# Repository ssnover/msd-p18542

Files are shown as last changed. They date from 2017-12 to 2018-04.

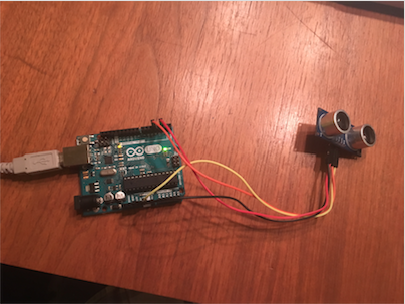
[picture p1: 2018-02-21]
prototyping/HCSRO4_Example/HCSR04 Wiring.png

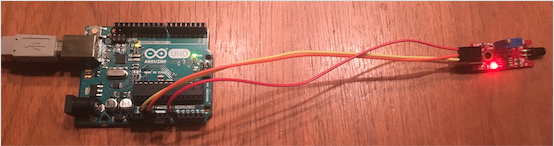
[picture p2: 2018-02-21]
prototyping/FlameSensor_Example/Flame sensor wiring.png

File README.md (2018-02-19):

# msd-p18542
Repository for RIT MSD P18542 source code, schematics, and CAD models.
# P18542: Real Time Terrain Mapping
In search and rescue operations time is often of the essence and the terrain can end up being wildly different than expected. The ability to image a landscape and use this data to determine the quickest route for operatives driving vehicles in this changing terrain in real-time could save lives in these scenarios. The goal of this project is to lay groundwork on this idea by imaging an area in real-time and using the image to plot route for a small autonomous vehicle.

## ASAR Robot
The first portion of this project consists of the electrical and PCB schematics for the robot along with mechanical CAD drawings and firmware for the Teensy 3.2 microcontroller development board.

### ASAR Teensy Firmware
The source code for the applications running on the Teensy is written for C++11 and will be made up of three primary applications run on a system tick:
1. Search and Rescue - controls search for the survivor and collection of data
2. Locomotion - controls movement of the robot
3. Command Manager - interfaces to the ASAR Aerial Platform to receive commands

## ASAR Aerial Platform
The second major portion of the project is a series of Python 3 modules run on a Raspberry Pi 3. These present a GUI for running the simulation and algorithms related to the computer vision and path finding aspects of the project. The major components include:
1. `asar-camera-engine` - Interface to the Raspberry Pi Camera
2. `asar-vision` - Generates a terrain map model from images
3. asar-path-finder - Takes the map model and finds the quickest path between two points
4. asar-web-ui - A web app hosted on the Pi to act as a GUI
5. asar-comms-server - Interface to the Pi's hardware UART
6. asar-core - The application the controls the flow of data between all of the above

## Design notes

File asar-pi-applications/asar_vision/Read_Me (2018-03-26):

# _Automatic Image Processing_ 
**Calibration Routine**
* This needs to be ran at the very beginning of a simulation.
* The calibration routine will walk you through clicking each individual color as well as the corners of the terrain in case of automation failure
* Once the calibration is done, the values printed out for color need to be input into the "Get RGB code"
* The corners of the terrain need to be input into the destination points backup for the homography
* This only needs to be done once unless the camera is bumped moving it significantly from its original position.

**Homography Automated**
* This is the main script that can be called.
* Within this file, all of the attributes of the terrain will be found and returned.
* An image is received from the raspberry pi that will the be processed. 
* After all processing is done, the tile attributes will be packaged into a json file named "Terrain.txt" and then sent to the path planning algorithm.

**Four Corners**
* The four corners of the terrain are automatically identified and marked as the source points for the image perspective transformation.
* This is where the hardcoded values that were obtained in the calibration routine will be held in the case that the corners are not able to be automatically found.

**Get Attributes**
* This script is responsible for finding all important parameters of the terrain.
* Within it, the color and coordinates of each tile are found.

**Get Coordinates**
* This script takes in the pixel values of each centroid of the hexagons within the terrain and classifies them as specific coordinats (1-8,1-8) on the grid for easier referencing.
* Once all nodes are classified, the coordinated values are added to the "coordinate" key in the hexagon attribute dictionary.

**Get RGB Color**
* This script gets the average pixel color value in the center of each identified hexagon
* Once the average HSV pixel color is found, it is converted to RGB and classified as one of the predetermined colors that were found in the calibration routine.
* The identified colors are added to the "Color" key within the hexagon attributes dictionary.

**Get Missing Terrain**
* This script looks at the coordinate list that was made by identifying hexagons on the terrain and compares it to the ideal coordinate list where all hexagons are found.
* If there are any missing points, the coordinate list is appended with the missing value and the color list is appended with an impassable terrain. If we dont know what is there, we cannot travel through it safely.

**Detect Shapes**
* This is the script responsible for finding the shapes within the terrain by finding the contour and counting the verticies.

**Shape Detection Test**
* If the shapes are not being identified, you can see exactly what the camera is seeing by running the image through this test script.

**Real Time HSV Codes**
* When Making masks, this script can be used to see what the mask will do block out or pass. The slider bars on the top are used to adjust the HSV values.

**Converter**
* This is used to make the upper and lower bounds of the masks that you make using the real time HSV code script.

**Utils**
* This allows you to clock the image in the calibration routine and have it return the values for the four corners to you as well as showing you where you clicked.

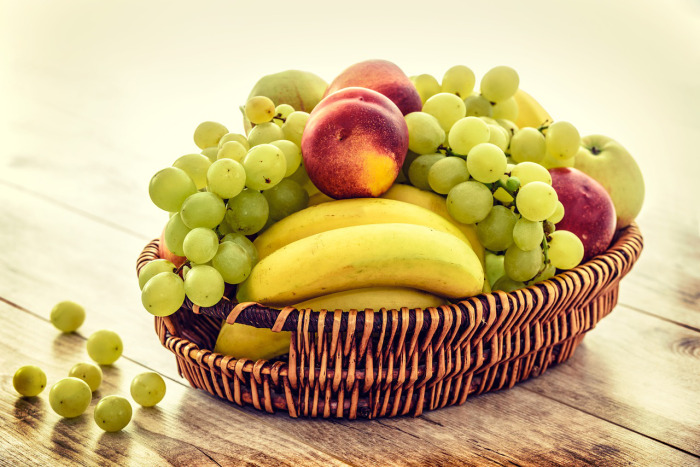
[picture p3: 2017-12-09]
prototyping/OpenCv/FruitBasket.jpg

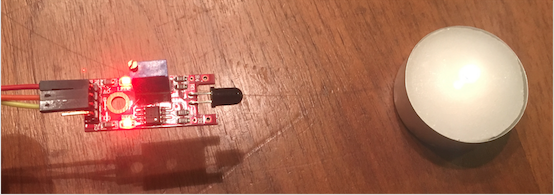
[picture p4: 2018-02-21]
prototyping/FlameSensor_Example/Flame detected.png

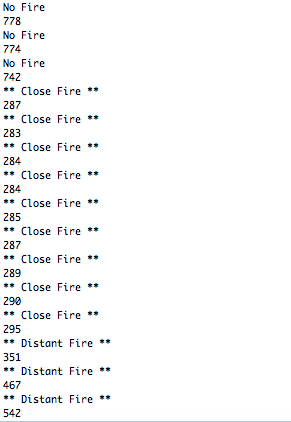
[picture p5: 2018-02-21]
prototyping/FlameSensor_Example/Flame Sensor Serial Output.png

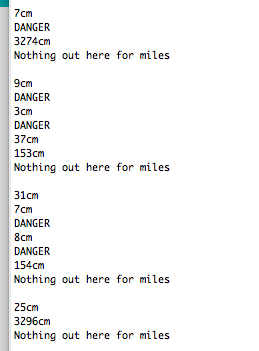
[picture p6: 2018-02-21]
prototyping/HCSRO4_Example/Ultrasonic Serial Output Example.png

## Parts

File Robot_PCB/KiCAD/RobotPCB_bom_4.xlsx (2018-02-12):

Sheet: imported
Component | Description | Part | References | Value | Footprint | Quantity Per PCB | Datasheet | P/N | MFG | Decription | Cost | Descrpition
1 | Unpolarized capacitor | C | C2 C3 | .1uF | C_1206_HandSoldering | 2 |  | GRM319R71H104KA01D | Murata | CAP CER 0.1UF 50V X7R 1206 | 0.26
2 | CAP CER 0.33UF 50V X7R 1206 | C | C1 | .33uF | C_1206_HandSoldering | 1 |  | GRM319R71H334KA01D | MURATA |  | 0.44
3 | LED GRN DIFF 5MM ROUND T/H | LED | D1 D2 D3 D4 | LED_GRN | LED_D5.0mm | 4 |  | LTL-4233 | Lite-On Inc. |  | 0.36
4 | PTC RESET FUSE 16V 2A RADIAL | Fuse | F1 F2 F3 F4 | 16V_2A | RHEF100 | 4 |  | RHEF200 | Littlefuse Inc. |  | 0.6
5 | CONN HEADER FEMALE 14POS.1" TIN | CON14_TeensyLeft | J1 | CON14_TeensyLeft | Socket_Strip_Straight_1x14_Pitch2.54mm | 1 |  | PPTC141LFBN-RC | Sullins Connector |  | 0.91
6 | CONN HEADER FEMALE 14POS.1" TIN | CON14_TeensyRight | J2 | CON14_TeensyRight | Socket_Strip_Straight_1x14_Pitch2.54mm | 1 |  | PPTC141LFBN-RC | Sullins Connector |  | 0.91
7 | CONN HEADER PH TOP 2POS 2MM | CON2_Battery | J11 | CON2_Battery | JST_PH_B2B-PH-K_02x2.00mm_Straight | 1 |  | B2B-PH-K-S(LF)(SN | JST Sales America Inc |  | 0.17
8 | CONN HEADER RTANG 2POS PCB TIN | CON2_DC-MOTOR | J7 J8 | CON2_DC-MOTOR | 5-103634-1 | 2 |  | 5-103634-1 | TE Connectivity |  | 0.73
9 | CONN HEADER RTANG 3POS PCB TIN | CON3_Servo | J9 | CON3_Servo | 5-103634-2 | 1 |  | 5-103634-2 | TE Connectivity |  | 1.11
10 | CONN HEADER RTANG 5POS PCB TIN | CON5_HC-SR04 | J3 | CON5_HC-SR04 | 5-103634-4 | 1 |  | 5-103634-4 | TE Connectivity |  | 1.32
11 | CONN HEADER FEM 5POS .1" SGL TIN | CON5_XBEE | J10 | CON5_XBEE | Socket_Strip_Straight_1x05_Pitch2.54mm | 1 |  | PPTC051LFBN-RC | Sullins Connector |  | 0.47
12 | CONN HEADER RTANG 6POS PCB TIN | CON6_M-Encoder | J5 J6 | CON6_M-Encoder | 5-103634-5 | 2 |  | 5-103634-5 | TE Connectivity |  | 1.4
13 | CONN HEADER RTANG 4POS PCB TIN | Con4_FlameSensor | J4 | Con4_FlameSensor | 5-103634-3 | 1 |  | 5-103634-3 | TE Connectivity |  | 1.3
14 | CONN HEADER .100" SNGL STR 15POS | TestHeaders | J12 J13 | TestHeaders | Pin_Header_Straight_1x15_Pitch2.54mm | 2 |  | PRPC015SAAN-RC | Sullins Connector |  | 0.38
15 | RES SMD 0 OHM JUMPER 1/4W 1206 | R | R6 R7 | R_0 | R_1206_HandSoldering | 2 |  | RC1206JR-070RL | Yageo |  | 0.1
16 | RES SMD 150 OHM 5% 1/4W 1206 | R | R3 | R_150 | R_1206_HandSoldering | 1 |  | RC1206JR-07150RL | Yageo |  | 0.1
17 | Resistor | R | R1 R2 | R_1K | R_1206_HandSoldering | 2 |  | RC1206JR-071KL | Yageo |  | 0.1 | RES SMD 1K OHM 5% 1/4W 1206
18 | RES SMD 59 OHM 1% 1/4W 1206 | R | R4 R5 | R_59 | R_1206_HandSoldering | 2 |  | RC1206FR-0759RL | Yageo |  | 0.1
19 | AUDIO PIEZO TRANSDUCER 30V TH | Speaker | SP1 | Speaker | BUZZER | 1 |  | PS1240P02BT | TDK |  | 0.72
20 | SWITCH TOGGLE SPDT 5A 120V | SW_SPST | SW1 | SW_SPST | WireConnection_1.20mmDrill | 1 |  | 100SP1T1B1M1QEH | E-Switch |  | 2.11
21 | IC MOTOR DRIVER PAR 16-DIP | L293D | U2 | L293D | L293D | 1 |  | L293D | ST Microelectronics |  | 3.91
22 | IC REG LINEAR 5V 1.5A TO220AB | L7805 | U1 | L7805 | TO-220 | 1 | http://www.st.com/content/ccc/resource/technical/document/datasheet/41/4f/b3/b0/12/d4/47/88/CD00000444.pdf/files/CD00000444.pdf/jcr:content/translations/en.CD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 | L7805CV | STMicroelectronics |  | 0.45
Component Groups: | 22
Component Count: | 35
Fitted Components: | 35
Number of PCBs: | 1
Total components: | 35
Schematic Version: | 4
Schematic Date: | 2018-02-07
BoM Date: | 2018-02-12 14:37
Schematic Source: | C:/Users/ME/Documents/School/Spring_2018/Senior Design/Schematic/Kicad/RobotPCB.sch
KiCad Version: | Eeschema 4.0.7

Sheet: Better BOM
Board
 | Component | Quantity | References | Value | P/N | MFG | Cost | Ext. Cost
 | 1 | 2 | C2 C3 | .1uF | GRM319R71H104KA01D | Murata | $0.26 | $0.52
 | 2 | 1 | C1 | .33uF | GRM319R71H334KA01D | MURATA | $0.44 | $0.44
 | 3 | 4 | D1 D2 D3 D4 | LED_GRN | LTL-4233 | Lite-On Inc. | $0.36 | $1.44
 | 4 | 4 | F1 F2 F3 F4 | 16V_2A | RHEF200 | Littlefuse Inc. | $0.60 | $2.40
 | 5 | 1 | J1 | CON14_TeensyLeft | PPTC141LFBN-RC | Sullins Connector | $0.91 | $0.91
 | 6 | 1 | J2 | CON14_TeensyRight | PPTC141LFBN-RC | Sullins Connector | $0.91 | $0.91
 | 7 | 1 | J11 | CON2_Battery | B2B-PH-K-S(LF)(SN | JST Sales America Inc | $0.17 | $0.17
 | 8 | DNI | J7 J8 | CON2_DC-MOTOR | 5-103634-1 | TE Connectivity | $0.73 | $0.00
 | 9 | 1 | J9 | CON3_Servo | 5-103634-2 | TE Connectivity | $1.13 | $1.13
 | 10 | 1 | J3 | CON5_HC-SR04 | 5-103634-4 | TE Connectivity | $1.34 | $1.34
 | 11 | 1 | J10 | CON5_XBEE | PPTC051LFBN-RC | Sullins Connector | $0.47 | $0.47
 | 12 | 2 | J5 J6 | CON6_M-Encoder | 5-103634-5 | TE Connectivity | $1.47 | $2.94
 | 13 | 1 | J4 | Con4_FlameSensor | 5-103634-3 | TE Connectivity | $1.32 | $1.32
 | 14 | 2 | J12 J13 | TestHeaders | PRPC015SAAN-RC | Sullins Connector | $0.38 | $0.76
 | 15 | 2 | R6 R7 | R_0 | RC1206JR-070RL | Yageo | $0.10 | $0.20
 | 16 | 1 | R3 | R_150 | RC1206JR-07150RL | Yageo | $0.10 | $0.10
 | 17 | 2 | R1 R2 | R_1K | RC1206JR-071KL | Yageo | $0.10 | $0.20
 | 18 | 2 | R4 R5 | R_59 | RC1206FR-0759RL | Yageo | $0.10 | $0.20
 | 19 | 1 | SP1 | Speaker | PS1240P02BT | TDK | $0.72 | $0.72
 | 20 | 1 | SW1 | SW_SPST | 100SP1T1B1M1QEH | E-Switch | $2.11 | $2.11
 | 21 | 1 | U2 | L293D | L293D | ST Microelectronics | $3.91 | $3.91
 | 22 | 1 | U1 | L7805 | L7805CV | STMicroelectronics | $0.57 | $0.57
 |  |  |  |  |  |  | Board total | $22.76
Cables
 | Cable | Part | MFG | MFG # | Quantity per cable | Cost ea | Ext Cost per cable | Total Quantity | Total Cost
 | Motor (x2)
 |  | Female Pins | TE Connectivity | 1-104480-7 | 6 | 0.164 | $0.98 | 12 | $1.97
 |  | 6p Female Header | TE Connectivity | 104257-5 | 1 | 0.68 | $0.68 | 2 | $1.36
 | HC-SR04
 |  | Female Pins | TE Connectivity | 1-104480-7 | 4 | 0.164 | $0.66 | 4 | $0.66
 |  | 5P Female Header | TE Connectivity | 104257-4 | 1 | 0.6 | $0.60 | 1 | $0.60
 | Flame Sensor
 |  | Female Pins | TE Connectivity | 1-104480-7 | 4 | 0.164 | $0.66 | 4 | $0.66
 |  | 4P Female Header | TE Connectivity | 104257-3 | 1 | 0.58 | $0.58 | 1 | $0.58
 | Servo
 |  | Female Pins | TE Connectivity | 1-104480-7 | 3 | 0.164 | $0.49 | 3 | $0.49
 |  | 3P Header | TE Connectivity | 104257-3 | 1 | 0.52 | $0.52 | 1 | $0.52
 | Battery
 |  | Female Pins | JST | SPH-002T-P0.5L | 2 | 0.1 | $0.20 | 2 | $0.20
 |  | Female Housing | JST | PHR-2 | 1 | 0.1 | $0.10 | 1 | $0.10
 |  |  |  |  |  |  |  | Total Cable Cost | $7.13
 |  |  |  |  |  |  | Total | $29.89
 | Cable Totals | Part | MFG | P/N | Quatity | Cost | Ext Cost
 |  | Female Pins | TE Connectivity | 1-104480-7 | 23 | 0.164 | $3.77
 |  | Female pins | JST | SPH-002T-P0.5L | 2 | 0.1 | $0.20
 |  | 6p header | TE Connectivity | 104257-5 | 2 | 0.68 | $1.36
 |  | 5p header | TE Connectivity | 104257-4 | 1 | 0.6 | $0.60
 |  | 4p header | TE Connectivity | 104257-3 | 1 | 0.58 | $0.58
 |  | 3pheader | TE Connectivity | 104257-2 | 1 | 0.52 | $0.52
 |  | 2p header | JST | PHR-2 | 1 | 0.1 | $0.10
 |  |  |  |  |  | Total | $7.13

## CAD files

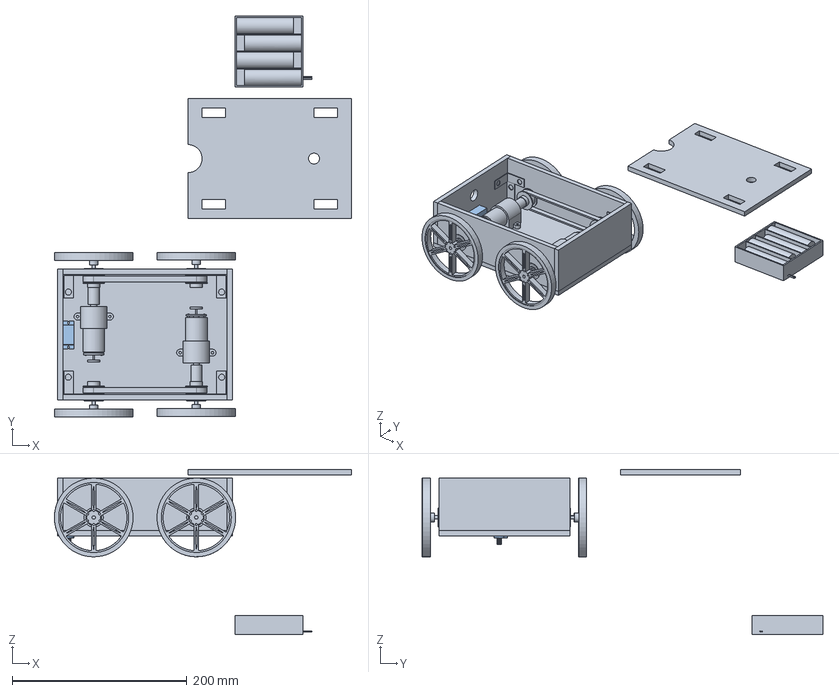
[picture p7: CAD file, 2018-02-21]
Robot-Design/Assembly 1 (1).step
339.8 x 458.4 x 188.8 mm
DriveShaft
ServoBody

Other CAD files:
Robot-Design/4mm ROD LONG.sldprt
Robot-Design/WHEEL HUB.sldprt
Robot-Design/SHAFT COUPLER.sldprt
Robot-Design/BACK WALL (1).sldprt
Robot-Design/TIMING BELT PULLEY.sldprt
Robot-Design/MOTOR MOUNT.sldprt
Robot-Design/BEARING.sldprt
Robot-Design/SIDE WALLS (1).sldprt
Robot-Design/BASE (1).sldprt
Robot-Design/L-BRACKET.sldprt
Robot-Design/4mm ROD SHORT.sldprt
Robot-Design/SHELF.sldprt
Robot-Design/FRONT WALL (1).sldprt
Robot-Design/TIMING BELT.sldprt
Robot-Design/WHEELS.sldprt
Robot-Design/BEARING AXEL FITTING.sldprt
Robot-Design/MOTOR 34-1.sldprt
Robot-Design/18650 4S Battery Holder.sldprt

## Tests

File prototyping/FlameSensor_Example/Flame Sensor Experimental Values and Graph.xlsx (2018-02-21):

Distance | Analog Reading 1 | Analog Reading 2 | Analog Reading 3 | Analog Reading 4 | Analog Reading
5 | 288 | 285 | 283 | 284 | 285
10 | 289 | 289 | 290 | 292 | 290
15 | 301 | 299 | 296 | 295 | 297.75
20 | 301 | 303 | 310 | 303 | 304.25
25 | 407 | 452 | 438 | 463 | 440
30 | 550 | 561 | 562 | 578 | 562.75
35 | 644 | 655 | 649 | 650 | 649.5

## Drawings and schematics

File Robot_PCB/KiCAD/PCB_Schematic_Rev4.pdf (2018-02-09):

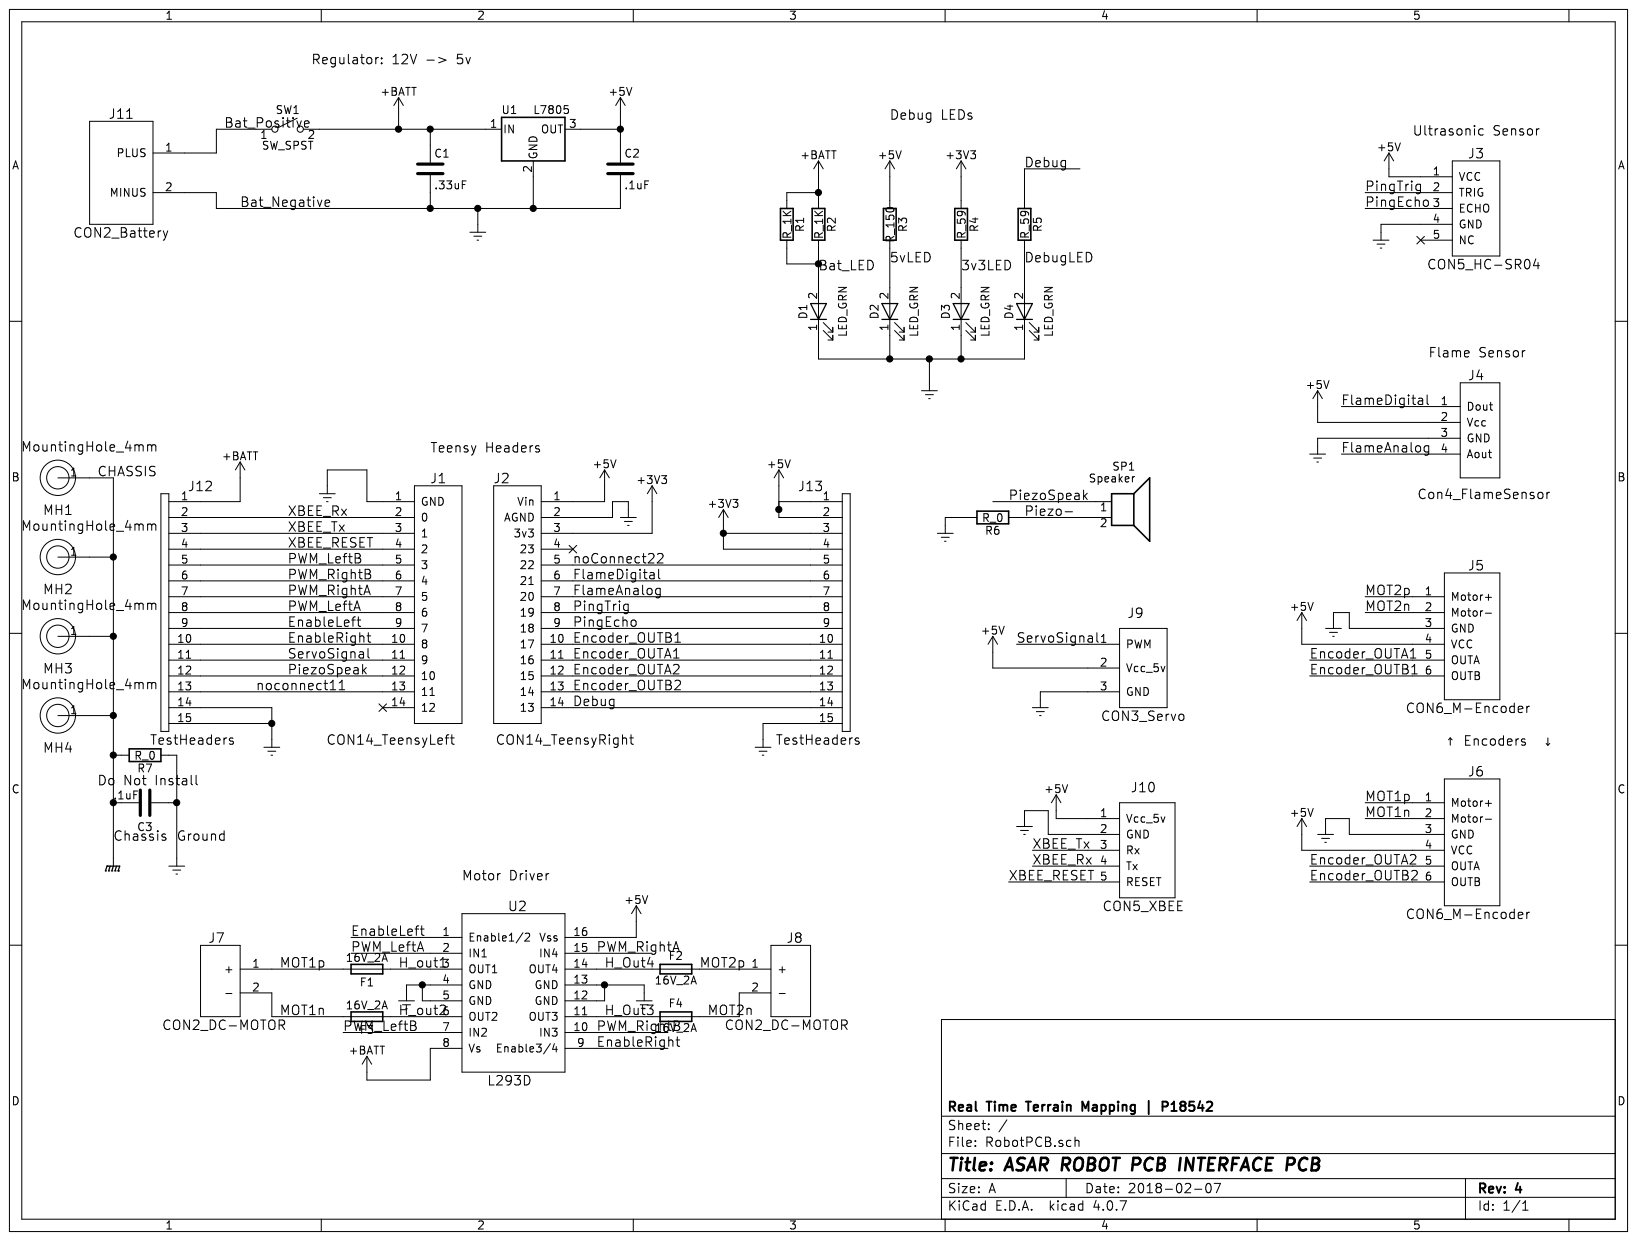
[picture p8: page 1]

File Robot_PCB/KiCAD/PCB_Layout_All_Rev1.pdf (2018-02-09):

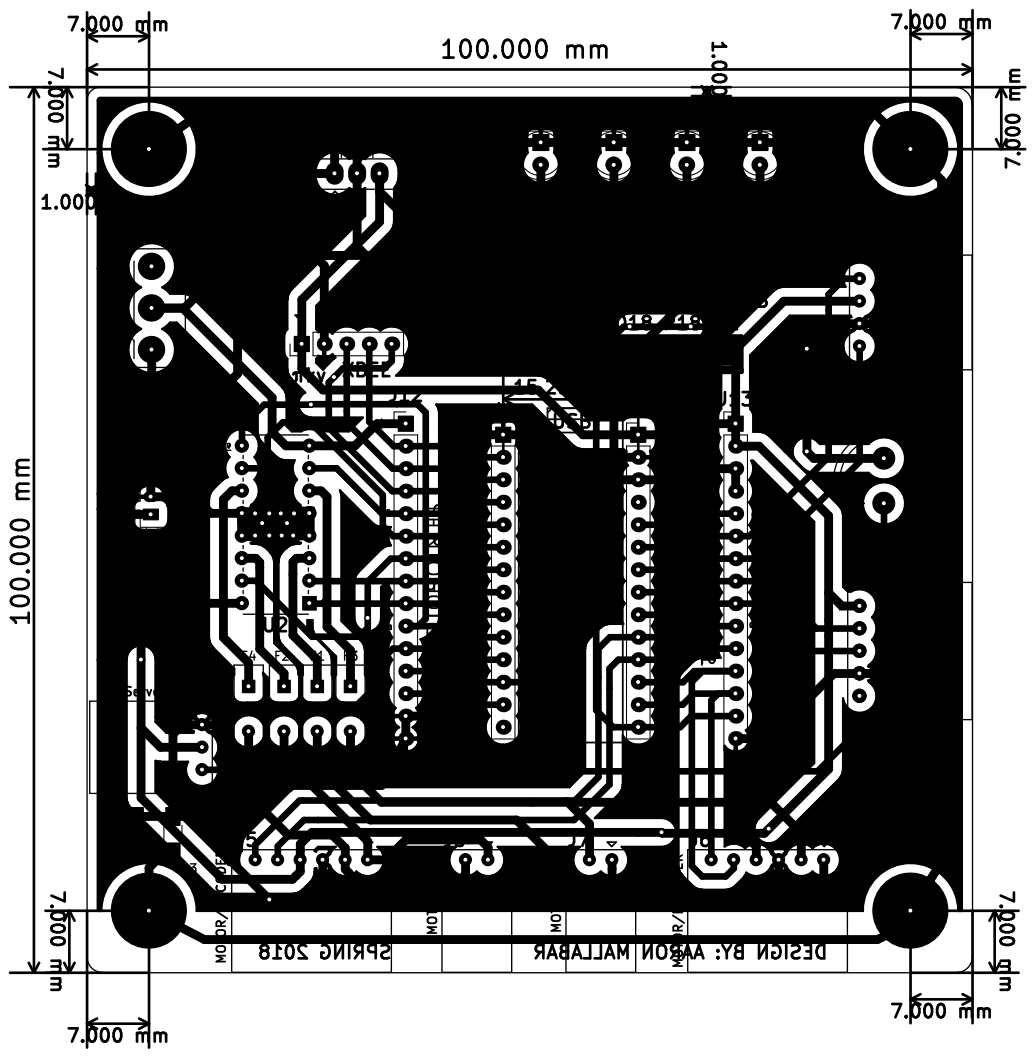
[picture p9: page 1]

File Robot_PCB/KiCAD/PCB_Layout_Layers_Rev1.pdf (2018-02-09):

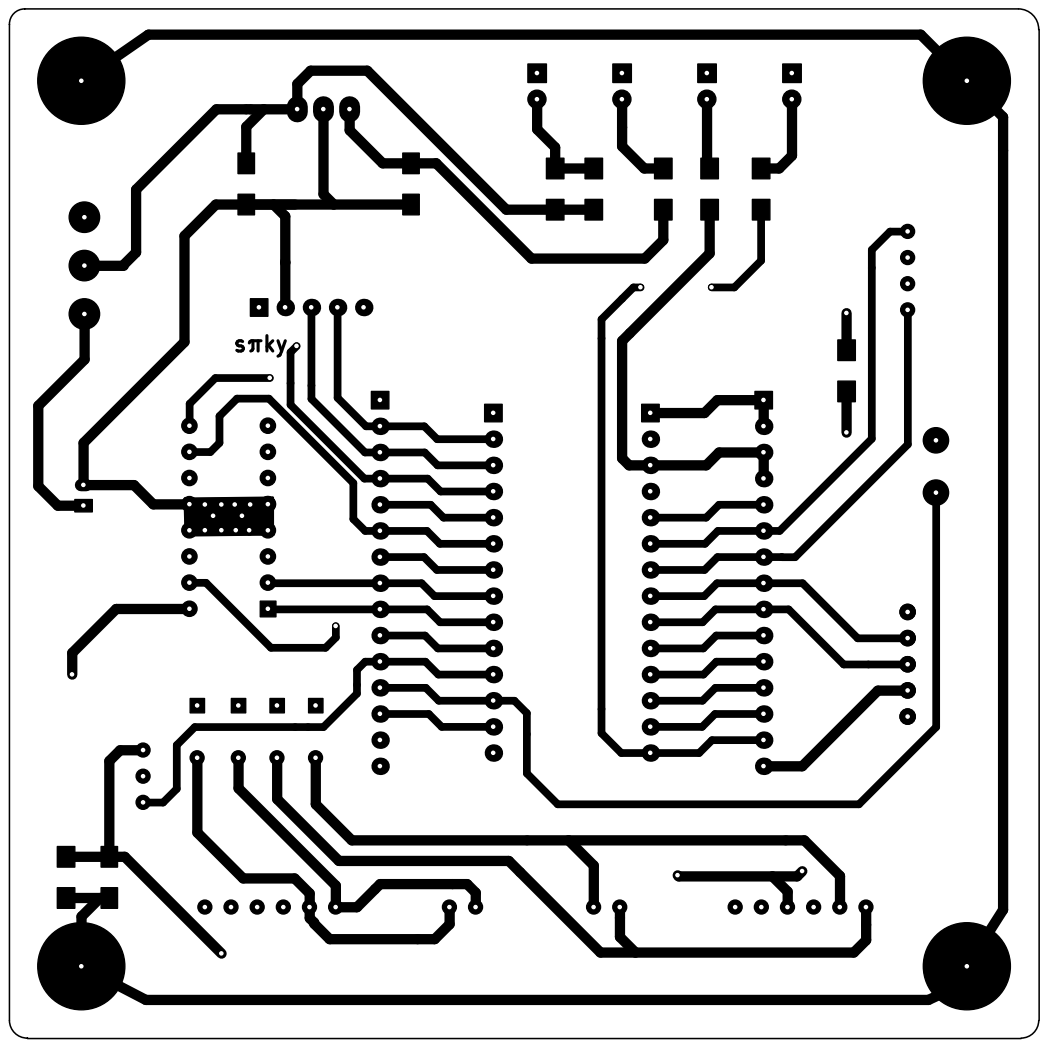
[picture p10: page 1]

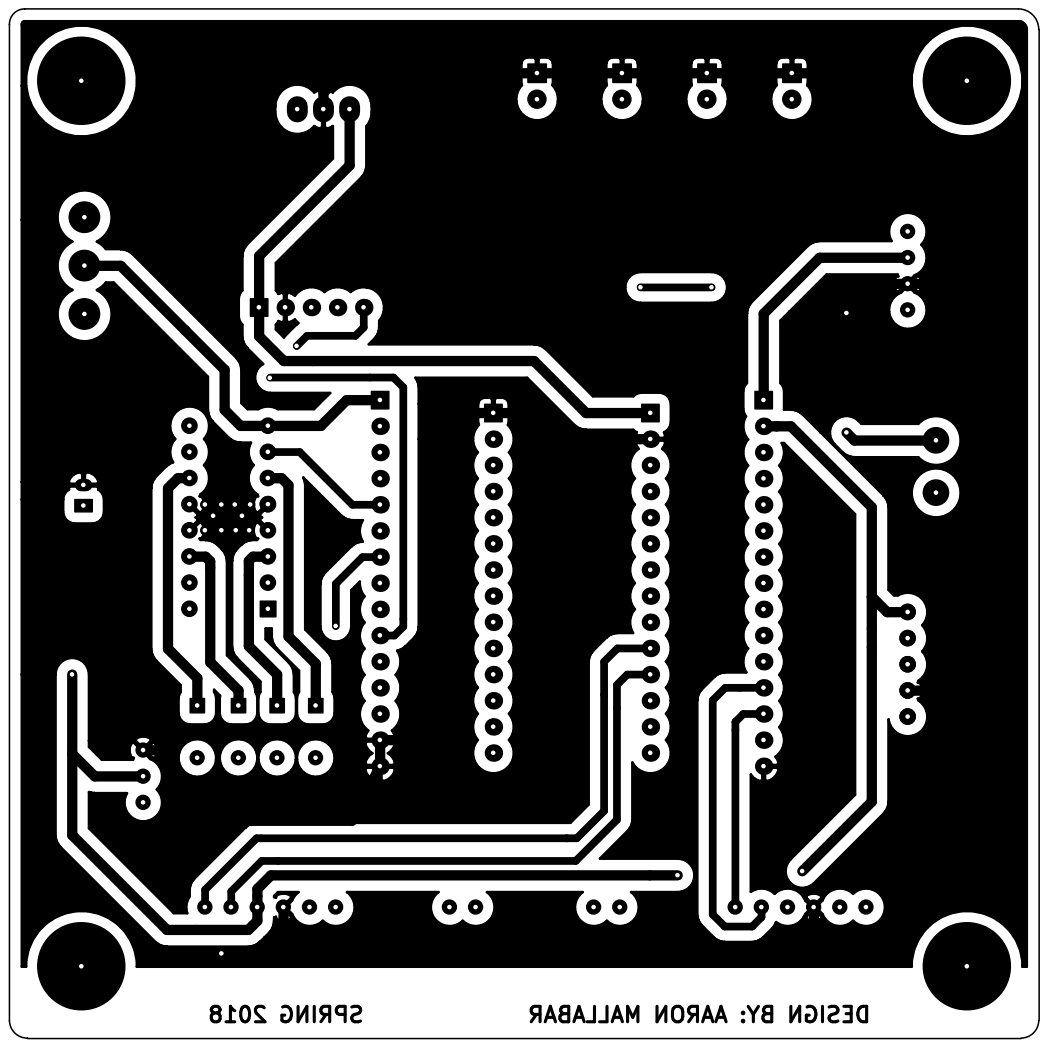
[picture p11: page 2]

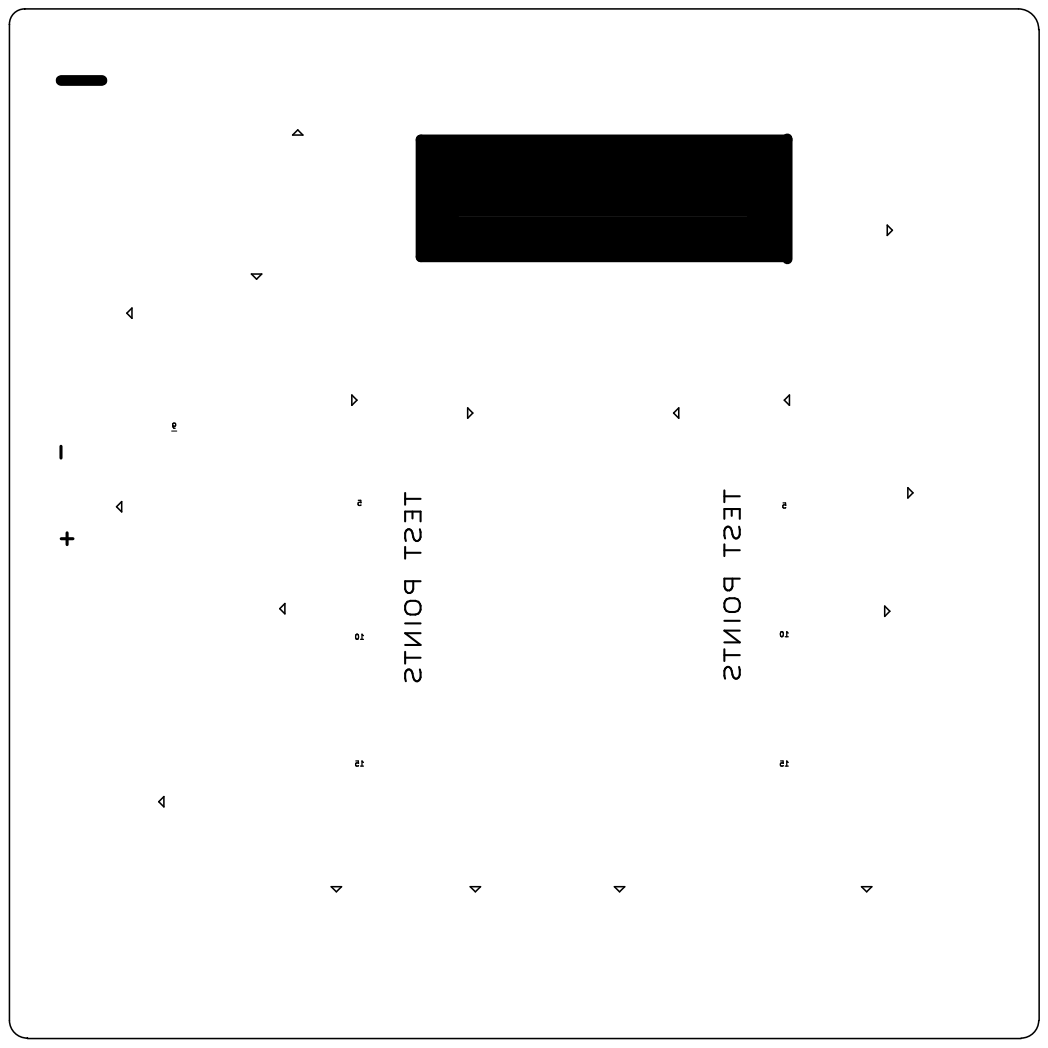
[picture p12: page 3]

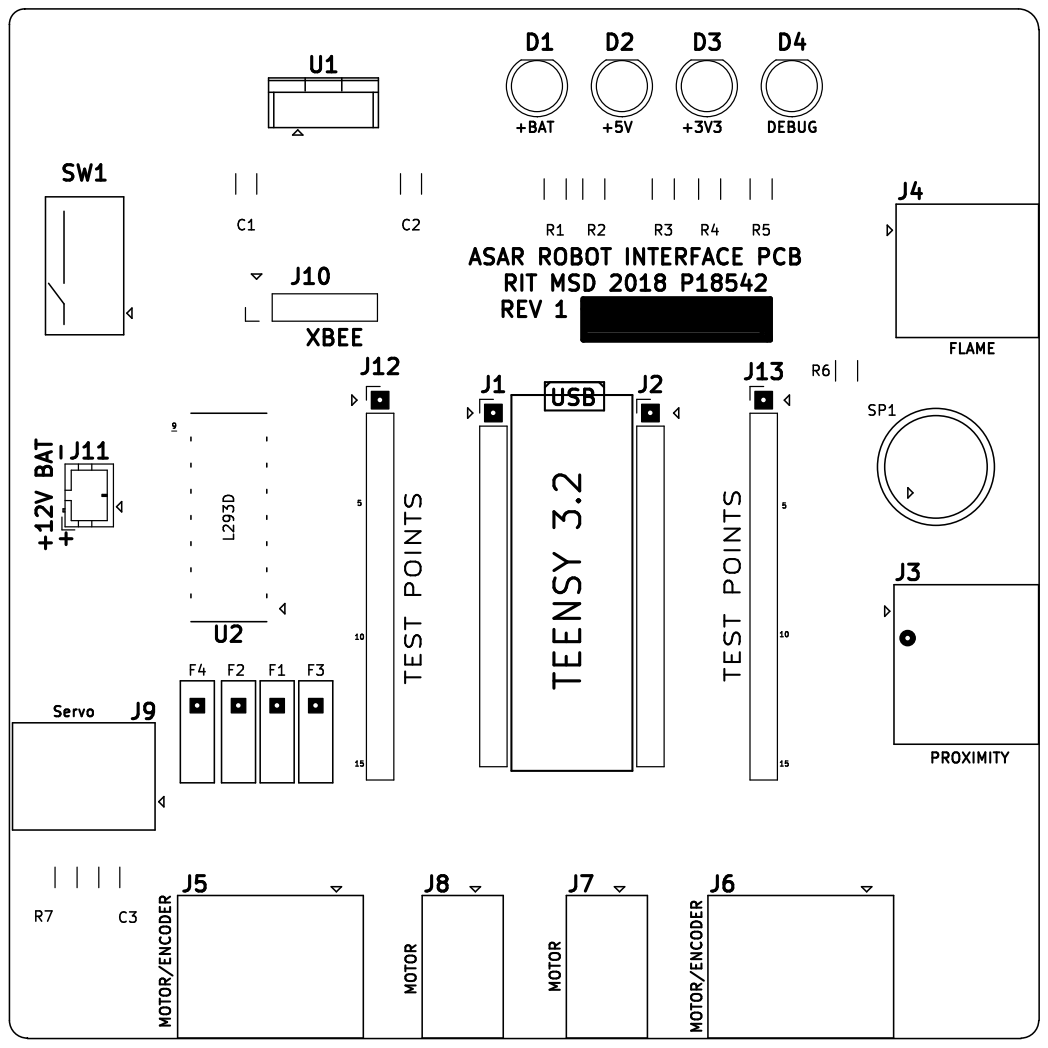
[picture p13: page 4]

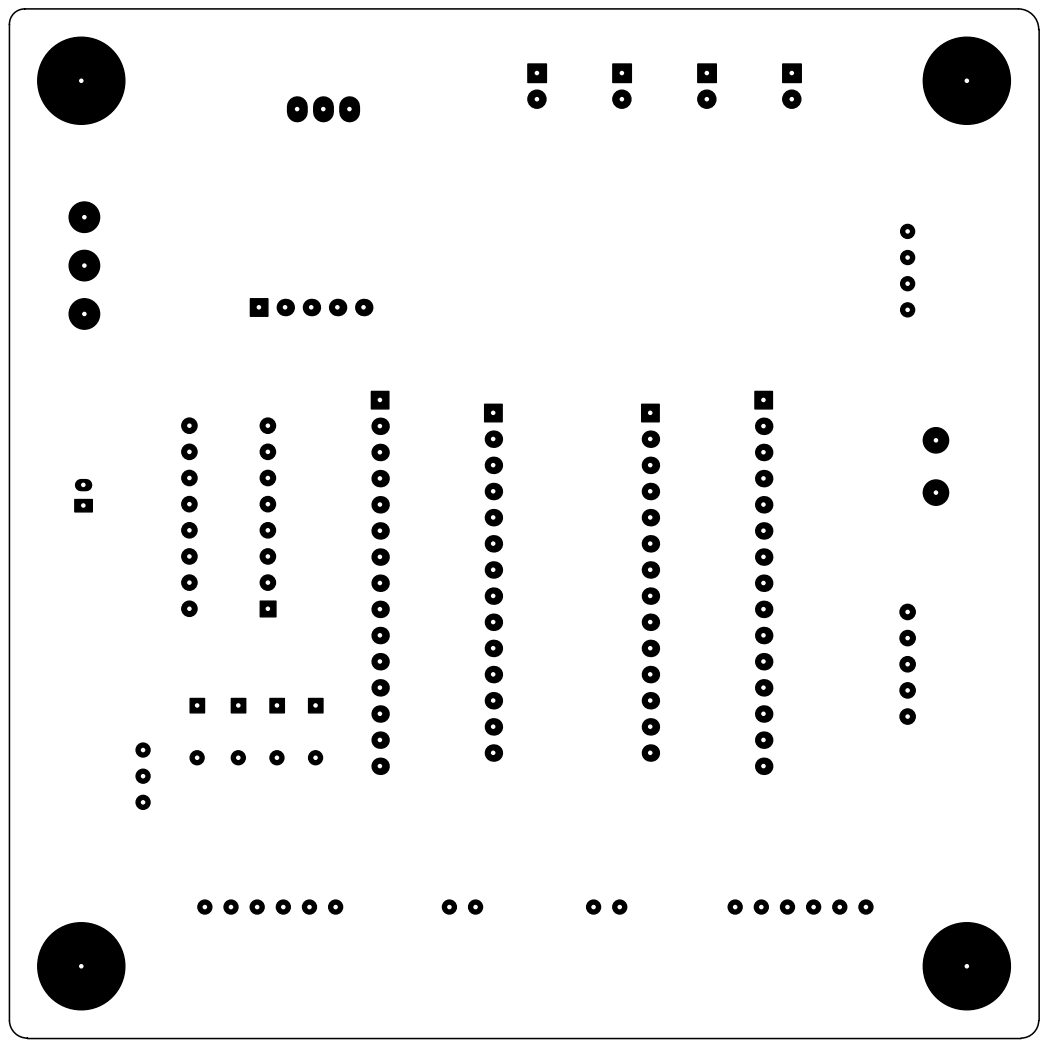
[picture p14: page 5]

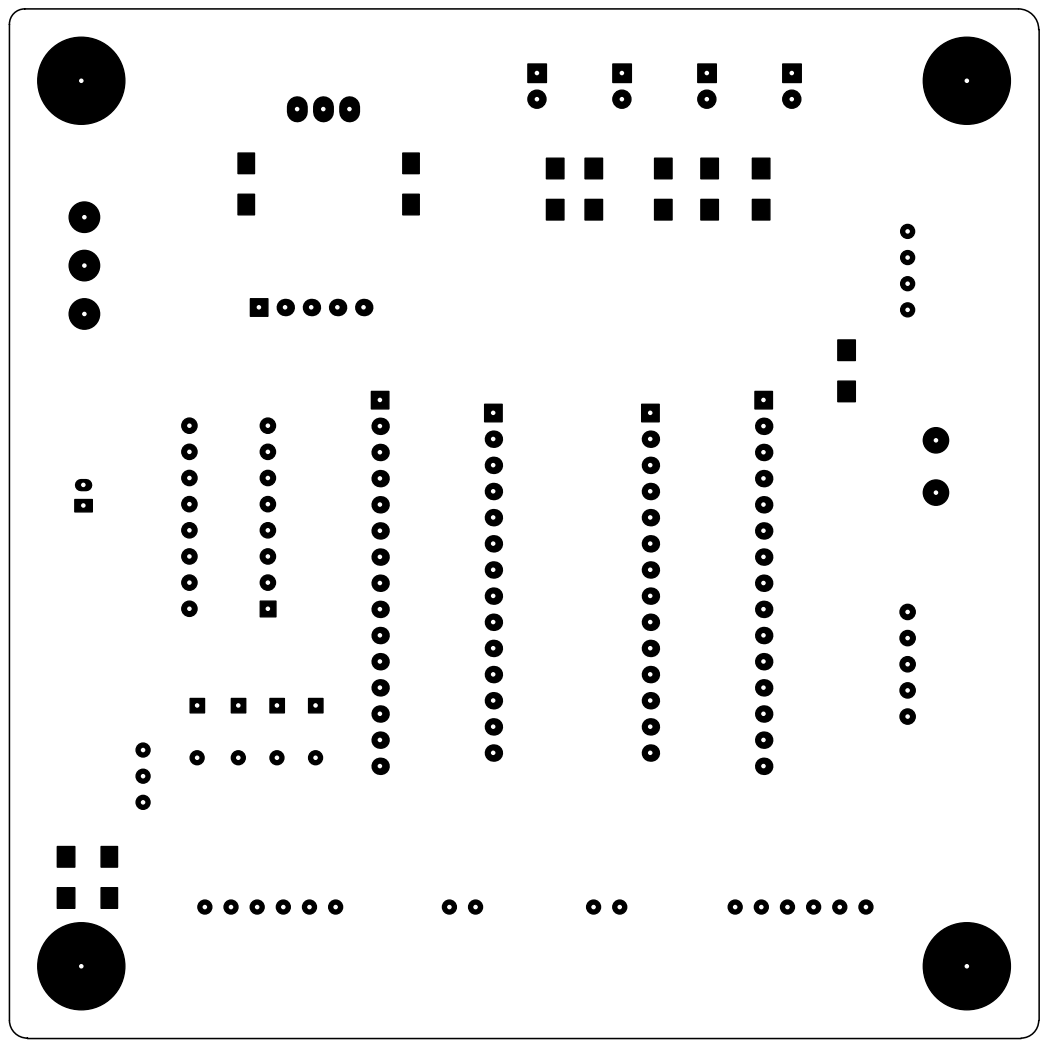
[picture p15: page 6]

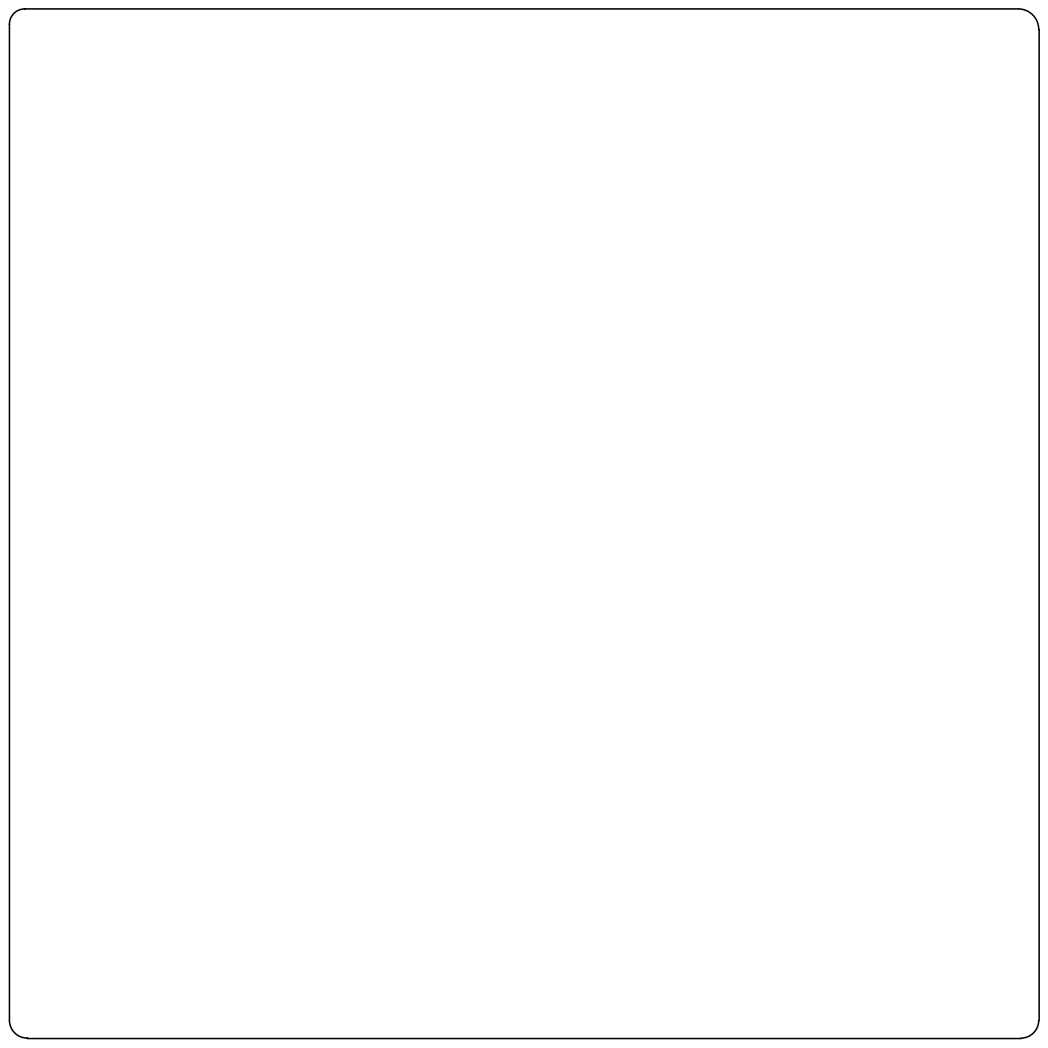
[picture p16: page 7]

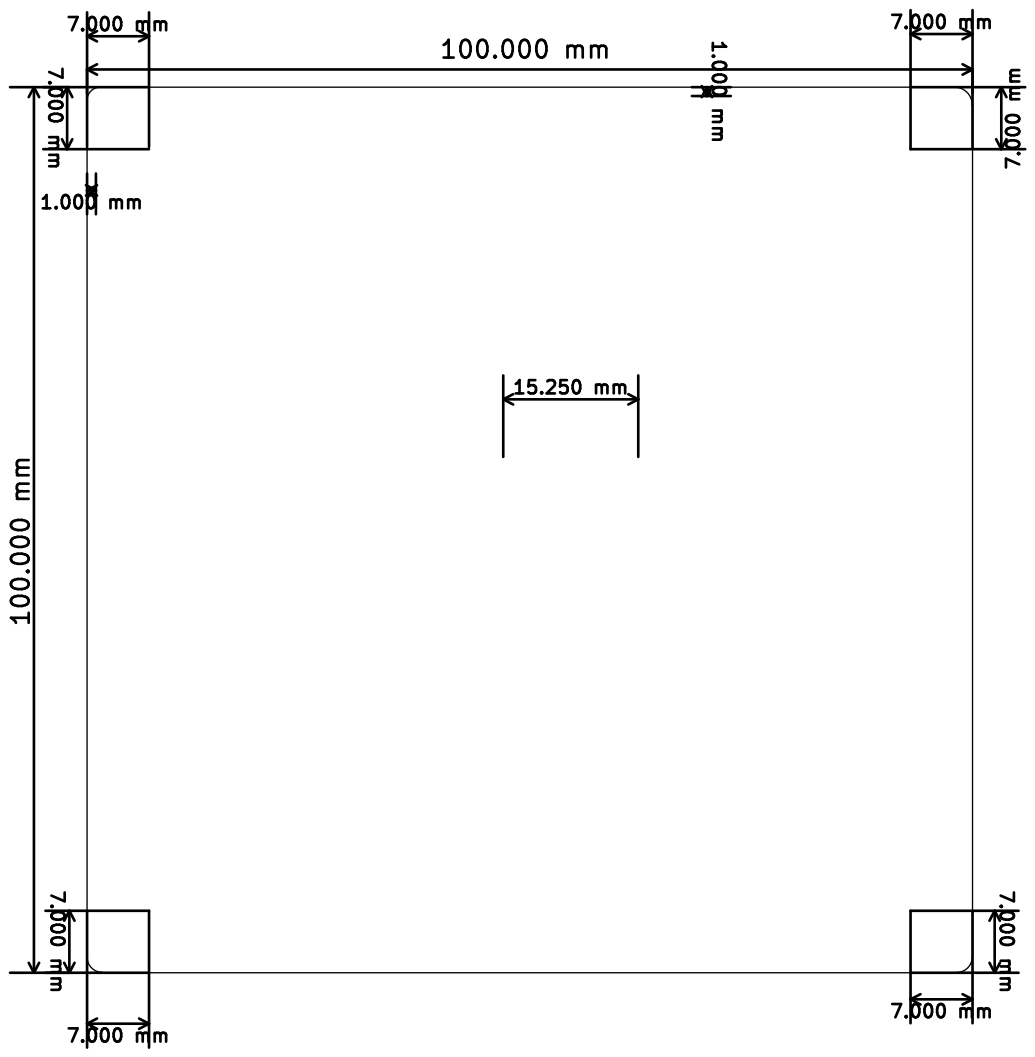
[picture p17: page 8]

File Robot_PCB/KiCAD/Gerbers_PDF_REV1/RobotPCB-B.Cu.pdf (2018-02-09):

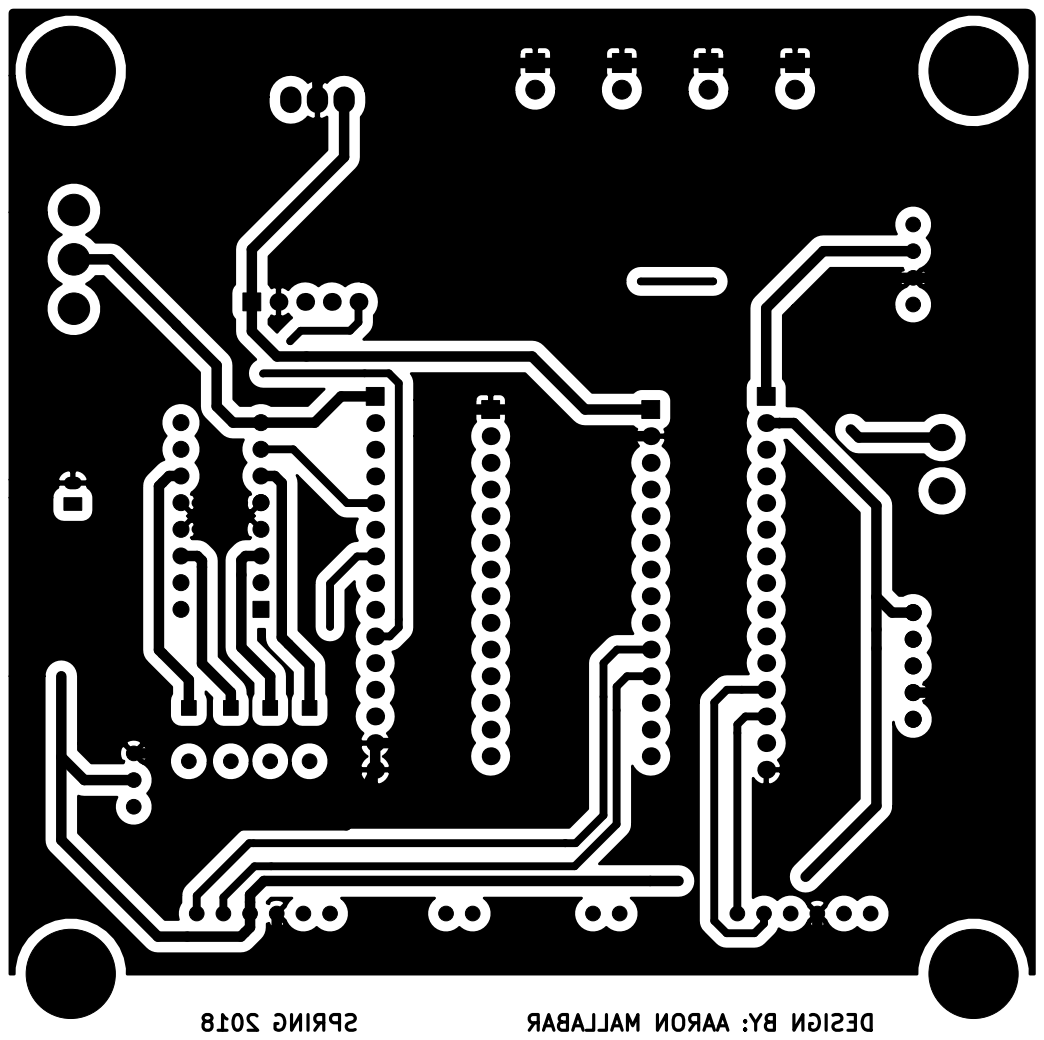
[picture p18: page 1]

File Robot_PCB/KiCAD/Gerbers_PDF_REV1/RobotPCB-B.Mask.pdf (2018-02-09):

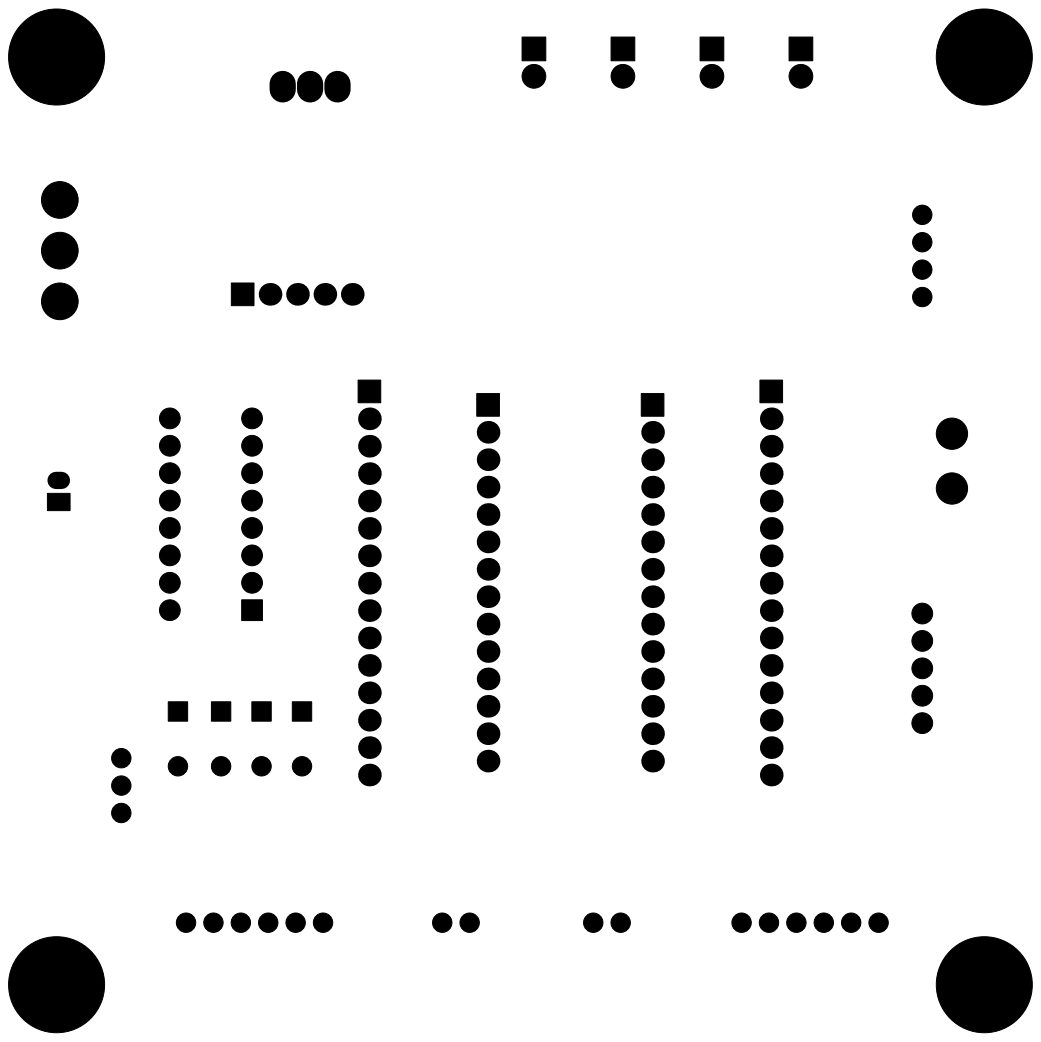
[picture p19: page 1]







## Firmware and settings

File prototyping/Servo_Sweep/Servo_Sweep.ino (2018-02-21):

Servo myservo;  // create servo object to control a servo
// twelve servo objects can be created on most boards

int pos = 0;    // variable to store the servo position

void setup() {
  myservo.attach(9);  // attaches the servo on pin 9 to the servo object
}

void loop() {
  for (pos = 0; pos <= 180; pos += 1) { // goes from 0 degrees to 180 degrees
    // in steps of 1 degree
    myservo.write(pos);              // tell servo to go to position in variable 'pos'
    delay(15);                       // waits 15ms for the servo to reach the position
  }
  for (pos = 180; pos >= 0; pos -= 1) { // goes from 180 degrees to 0 degrees
    myservo.write(pos);              // tell servo to go to position in variable 'pos'
    delay(15);                       // waits 15ms for the servo to reach the position
  }
}

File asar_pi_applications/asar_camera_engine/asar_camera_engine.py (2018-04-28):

#!/usr/bin/python3
"""
    file: asar-camera-engine.py
    purpose: Specifies the class for controlling and interfacing to the Raspberry Pi Camera.
"""

import datetime
import os
import sqlite3
import threading
import time


try:
    from picamera import PiCamera
except ImportError:
    print("PiCamera module is not installed.")
    quit()


class ASARCameraEngine:

    def __init__(self, frequency, database_store_call, image_path):
        """
        Constructor.
        """
        self.my_camera = PiCamera()
        self.my_capture_call = database_store_call
        self.my_images_directory = image_path
        self.my_capture_frequency = frequency
        self.my_worker_thread = threading.Thread(target=self.cameraEngineImageContext, args=())
        self.my_worker_thread.daemon = True
        self.my_running_status = False
        self.my_camera_is_busy = False

    def begin(self):
        """
        Start the thread controlling the ASAR camera engine.
        :return: Boolean representing the running state of the camera engine.
        """
        if self.my_camera_is_busy:
            return False
        self.my_running_status = True
        self.my_worker_thread.start()
        return True

    def end(self):
        """
        Stop the ASAR camera engine execution.
        :return: None.
        """
        print("Shutting down camera engine")
        self.my_running_status = False
        self.my_worker_thread.join()

    def takePicture(self):
        """
        Requests the engine to take a picture with the PiCamera.
        :return: Path to the image.
        """
        current_time = datetime.datetime.now()
        dt_string = '{:04d}'.format(current_time.year) \
                  + '{:02d}'.format(current_time.month) \
                  + '{:02d}'.format(current_time.day) \
                  + '_' \
                  + '{:02d}'.format(current_time.hour) \
                  + '{:02d}'.format(current_time.minute) \
                  + '{:02d}'.format(current_time.second) \
                  + '_' \
                  + '{:06d}'.format(current_time.microsecond)
        filename = dt_string + '.jpg'
        image_path = os.path.join(self.my_images_directory, filename)

        self.my_camera.capture(image_path, use_video_port=True)

        return image_path

    def takeVideo(self, path, length_in_seconds):
        """
        Requests the engine to take a video.
        :param path: The absolute path to the video file to create.
        :param length_in_seconds: Length of video to record in seconds.
        :return: Boolean of whether capture was started.
        """
        if path.split('.')[-1] != 'h264':
            return False
        if self.my_running_status:
            return False

        video_thread = threading.Thread(target=self.cameraEngineVideoContext,
                                        args=(path, length_in_seconds))
        video_thread.start()
        return True

    def cameraEngineImageContext(self):
        """
        Executed by the camera engine application to take a picture on a set rate.
        :return: None.
        """
        while self.my_running_status:
            print("Taking that picture!")
            # need to start putting image paths in database
            new_image_path = self.takePicture()

            time.sleep(1 / self.my_capture_frequency - 0.1)

    def cameraEngineVideoContext(self, path, length_in_seconds):
        """
        Executed by the camera engine application to take a video for a set
        amount of time.
        :param path: Path to store the video capture at.
        :param length_in_seconds:
        :return: None
        """
        self.my_camera_is_busy = True
        start_time = datetime.datetime.now()
        self.my_camera.start_recording(path)

        while (datetime.datetime.now() - start_time).seconds < length_in_seconds:
            pass

        self.my_camera.stop_recording()
        self.my_camera_is_busy = False


def main():
    """
    Entry point for testing.
    :return:
    """
    TOTAL_TIME_TO_RUN_SECONDS = 10
    CAPTURE_FREQUENCY_HZ = 2
    IMAGE_STORAGE_LOCATION = os.path.join(os.sep, 'home', 'pi', 'asar', 'images')

    my_camera = ASARCameraEngine(CAPTURE_FREQUENCY_HZ,
                                 os.path.join(os.sep, 'tmp', 'asar.db'),
                                 IMAGE_STORAGE_LOCATION)
    my_camera.begin()
    start_time = datetime.datetime.now()

    while (datetime.datetime.now() - start_time).seconds < TOTAL_TIME_TO_RUN_SECONDS:
        time.sleep(1)

    my_camera.end()

    for filename in os.listdir(IMAGE_STORAGE_LOCATION):
        if '.jpg' in filename:
            os.remove(os.path.join(IMAGE_STORAGE_LOCATION, filename))

    return 0


if __name__ == "__main__":
    main()

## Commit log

2017-11-13 Added prototyping for the wireless communications with the XBee.
2017-11-15 Fixed a function comment.
    [main.py]
2017-11-15 Created a socket wrapper and wrote simple code for the two sockets.
2017-11-15 Added a common source for prototypes.
2017-11-15 Add files via upload
    Rev 1 of the Schematic. Uses STM32.
    [MSD_ROBOT_BOARD.DSN]
2017-11-15 Moving Files Around
    [MSD_ROBOT_BOARD.DSN]
2017-11-30 REV2 Schematic Files: Uses TEENSY and XBEE
    [MSD_ROBOT_BOARD_REV2.DSN]
2017-12-06 Fixed edge case for 0x00. Made sketch for interpreting bytedata visually.
    [main.py, wireless-proto.ino]
2017-12-06 Added terminal switch for Pi.
2017-12-08 Fixed the device path for hardware UART on Pi. Tested and works.
    [main.py]
2017-12-08 Entry point for Teensy firmware.
2017-12-08 New Uploaded Files, Final for DDR
    [MSD_ROBOT_BOARD_REV2.DSN, MSD_ROBOT_BOARD_REV2.xlsx]
2018-01-08 KiCAD Files
    [RobotPCB.sch, RobotPCB_bom_3.xlsx]
2018-01-08 KiCAD Schematic
2018-01-08 deleted because of duplicates created trying to change the name
    [RobotPCB.sch, RobotPCB_bom_3.xlsx]
2018-01-13 Initial commit for asar-camera-engine application module.
2018-01-18 Initital Testing, BlinkLED Motor Forward
2018-01-18 Added Encoder Test
2018-01-22 Remove outdated schematic PDF
2018-01-22 MotorClass File Added
2018-01-22 Add Motor.H, Motor.cpp and modified test script to test motor
2018-01-24 More Motor Tests and Blinky program
2018-02-09 Board Update to REV1 Package
    Schematic Rev3 -> Rev4
    Layout Rev1 Final
    (Still need to update Bom)
    [RobotPCB-B.Cu.gbl, RobotPCB-B.Mask.gbs, RobotPCB-B.SilkS.gbo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]
2018-02-12 Updated to Rev4 and Purchased BOM
    [RobotPCB_bom_3.xlsx, RobotPCB_bom_4.xlsx]
2018-02-14 Complete function definitions in ASAR camera engine class
2018-02-18 Base frame of front end
2018-02-18 Fix thread joining mistake
    [asar_camera_engine.py]
2018-02-18 Fixed concurrency issue while using threads, changed to video due to speed concerns in taking pictures
    [asar_camera_engine.py]
2018-02-19 Good blink on interrupt script for teensy (Replaced the one that only worked for uno
    [good_blink.ino]
2018-02-19 Working Test Script for Proximity Sensor
2018-02-19 Added comments to ping test script and added a quick piezo buzzer test script
    [melodyScript.ino]
2018-02-19 Added Servo Test Script that works
2018-02-19 Transformed Proximity Sensor testing into a class and script to test class -Seems to work
2018-02-19 Fixed some threading issues, added some checks
    [asar_comms_server.py]
2018-02-19 added a combined motor and proximity sensor test script
2018-02-21 Add robot part
    [MOTOR 34-1.sldprt]
2018-02-21 added remaining parts
    [18650 4S Battery Holder.sldprt, 4mm ROD LONG.sldprt, 4mm ROD SHORT.sldprt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]
2018-02-21 Added robot sensor prototypes
    [Flame Sensor Experimental Values and Graph(2).xlsx, Flame Sensor Experimental Values and Graph.xlsx]
2018-03-04 More imporvements to xbee_read, including to form it around actual inputs from path finding algorithm ends with print the set of hex values in serial monitor
2018-03-04 Added capability to check if test script works by printing instruction set to monitor. Compiled, not tested
2018-03-05 Working code that takes in string of bits that includes the set of instructions, parses out instructions and after reading everything prints instructions on serial monitor
2018-03-09 Encoder can read a distance now, tested by manually moving encoder. Forced it to work by making many variable public when they shouldnt be
2018-03-09 Fixed bug that forgot to take into account gear ratio
2018-03-09 Added functionality in test to run motor forward for a specified distance
2018-03-09 Attempt to put the motors, encoders, and xbee (getting instructions) together. Compiles, but doesnt work right. Bug that causes instruction arrays to not be filled correctly.
    [ExecuteInstructs.ino]
2018-03-20 Play, stop, and pause buttons work
2018-03-20 Back From Spring Break - Easy to see that only the first instruction is read
2018-03-22 Search Algorithm File and Sample Terrain
2018-03-23 added a simpler motor test routine
2018-03-24 This is working code, in other words it can read instructions once, and execute them. I have not worked on real time updating instructions yet
    [ExecuteInstructs.ino]
2018-03-25 changed speed to not have factor of 50, move motor by giving exact pwm value
2018-03-26 Simplified main loop by creating free functions to execute and print the instructions
2018-03-27 Added folder that contains all header and source files. Also changed MOTOR.h to motor.h, Execute_instructs was tested again successfully
2018-04-09 Calibration Setup
    Pulled all calibratable constants and heuristic functions for the push to master. Calibration file for Pi will be added in parallel to this update
2018-04-09 Created Pi_Cfg.py
    This file contains all calibration variables and functions for the heuristic and robot instruction conversion functions.
2018-04-13 Added updating instruction functionality, tested communication with Pi, deleted outdated schematic
2018-04-14 Update per the Pull request code review
    mostly formatting, made debugging "print" to log file instead of terminal, added custom error codes
2018-04-14 added search.log as debug file
    this is a file that gets rewritten every time the code is run and prints the path in both coordinate and instruction protocol form for debugging
2018-04-15 Pre-test case evaluation Heuristic Overhaul
    Achieved behavioral functionality desired in last meeting
    updated euclidean to hexagonal Manhattan distance
2018-04-20 fixed updating instructions by restructuring main code
    [ExecuteInstructs.ino]
2018-04-26 updated for multiple thresholds
    [parameters.txt]
2018-04-26 parameters file
    [parameters.txt]
2018-04-26 param update
    [parameters.txt]
2018-04-28 actually works now
    [parameters.txt]
